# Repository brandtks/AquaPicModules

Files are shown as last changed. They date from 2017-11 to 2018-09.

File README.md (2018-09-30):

README
======
Board design and firmware for all modules used with the AquaPic Aquarium Controller. Each board should have corresponding firmware that works with that board version. All modules communicate with and are controlled by the [master controller/head unit](https://github.com/AquaPic/AquaPicController).

 * All PCB designs and layouts including gerber files are located under the _Boards_ directory. All PCB design is done using [KiCAD](http://kicad-pcb.org/). 
 * Firmware is located in the _Firmware_ directory. All the card's firmware should build without the need of the [MPLAB X IDE](http://www.microchip.com/mplab/mplab-x-ide), just the [XC compilers](http://www.microchip.com/mplab/compilers).
 * The _Documentation_ directory contains some useful information such as AquaPic Bus packets and other random notes.
 * Bill of materials are shared in [Google Drive](https://drive.google.com/drive/folders/1AOH0jgJ0CXvZnuD189EO4B9ZkvwggwkB?usp=sharing). 

### Status 
**IMPORTANT**: All modules are a work in progress. Most, if not all, are untested and very alpha quality.

### Website 
[HackADay Build Log](https://hackaday.io/project/1436-aquapic-aquarium-controller)

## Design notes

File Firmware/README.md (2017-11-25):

README
======
Firmware for the input/output cards for the AquaPic aquarium controller. Includes Analog Input and Output, Digital Input, and Power Strip stored in the projects directory. Libraries are included in the lib directory. This inludes the AquaPicBus slave driver, some common macros, and PIC16F specific drivers for ADC, UART, and PWM. All modules communicate with and are controlled by the [master controller/head unit](https://github.com/AquaPic/AquaPicController).

### Status
**IMPORTANT**: All modules are a work in progress. Most, if not all, are untested and very alpha quality.

### Toolchain
 * [Microchip XC8 v1.43](http://www.microchip.com/mplab/compilers); may work with early versions.
 * [Microchip XC32 v1.44](http://www.microchip.com/mplab/compilers); may work with early versions.

### Building
Edit Makefile-define.mk to match the executing environment and desired output paths, then exectute ```make```.

### License
The AquaPic firmware code is released under the terms of the GNU General Public License (GPL), version 3 or later. See COPYING for details.

### Website
 * [HackADay Build Log](https://hackaday.io/project/1436-aquapic-aquarium-controller)

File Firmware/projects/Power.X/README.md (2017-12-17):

README
======
Firmware for Power version 6. _libmmc.a_ contains the object files compiled from the code generated by the Microchip Code Configurator v3 utility. The object files were built used XC32 v1.44. 

### Status
**IMPORTANT**: Work in progress. Probably untested and very alpha quality.

### Website
 * [HackADay Build Log](https://hackaday.io/project/1436-aquapic-aquarium-controller)

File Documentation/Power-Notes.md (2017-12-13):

### Notes
 * Removed current measuring circuit from main control board, because it was a pain to design around. Instead, current monitoring will be done on a separate board that plugs into the control board.

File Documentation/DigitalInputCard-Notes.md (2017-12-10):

### Notes
 * The charlieplexed LEDs operate at 166.67Hz. This leads to each led being on for 1ms and off for 5ms.
 * The LEDs chosen have an forward voltage of approximately 3.1 V at 12 mA. 
 * With a 1/6 duty cycle the effective current will be 2 mA which results in a 20 mcd luminous intensity.

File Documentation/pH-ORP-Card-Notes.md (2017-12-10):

### Notes
 * The load resister on the output of the isolation power supply can and probably will be left off. Its there just in case stability is an issue.
 * The mosfet prior to each of the isolation power supplies provides a way to disable a channel when not in use thus limiting overall current draw.

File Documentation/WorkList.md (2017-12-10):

Bugs
=====================
 * Can't add modules, errors on address already used, only on the raspberry pi 
 * Move setup to init function and add input checking

Main Controller Software
========================
## Worklist 
 * Add way to change LPF constant for AI and pH/ORP
 * Enable/disable channels for pH
 * pH/ORP Scene
 * pH/ORP calibration
 * Refactor ATO to separate module
 * Add ATO scene
 * RO/DI module
 * Saltwater mixing module
 * Wave module
 * Add/Move widgets to home screen at runtime
 * Remove cards, power strips at runtime
 * Notifications
 * Tank maintenance scheduler
 * Runtime modules
 * Data logging on server
 * Backup/Store settings on database
 * Low priority - Lighting return to auto (ramp/hold to auto setpoint) and shutdown
 * _Maybe_ - Continue moving from list to dictionary in driver

Peripherals
===========
## Analog Input 
#### Firmware
 * Test on a board
 * Enable/disable channels
#### Hardware

## Analog Output
#### Firmware
 * Test on a board
#### Hardware
 * Test selectable output prior to manufacturing boards

## Digital Input
#### Firmware
 * Test on a board
#### Hardware

## pH/ORP 
#### Firmware
 * Test on a board
#### Hardware

## Power
#### Firmware
 * Refactor processor to PIC32MM0064GPM***
#### Hardware
 * Refactor processor to PIC32MM0064GPM***

Long Range Goals
================
 * Look at outlet current of heaters to determine what the setpoint of the heater is currently set at and then also check for stuck heater. 
 * Home server for data logging, and website. Home server will also issues commands to controller.
 * Pump control card
 * Water change module
 * Dosing Pumps
 * Feeding
 * Salinity
 * Function block programming
 * Move modules and GUI to ‘plugins’ that are added at runtime. This will allow the controller to be used for any sort of home automation such as home brewing, gardening, aquaponics. 
 * Over the “air” updates and boot loader for all slave modules

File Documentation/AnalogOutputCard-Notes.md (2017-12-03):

### Notes
 * The way the PWM(capture) module is implemented in the PIC32MM, there is a tradeoff between frequency and resolution. As the PWM frequency is increased, there is less range before the timer rolls over. To allow for changing the frequency in the firmware the main controller will send a value of 0 to 100 instead of some direct bit value. 
 * Currently the frequecy is set to 2Khz. With the capture module clocked to the system frequency at 24KHz, the timer rolls over at 0x4B0, 1200, i.e. 1200 bits of resolution.
 * CCPxRA will always remain at 0. CCPxRB is used to adjust the duty cycle.

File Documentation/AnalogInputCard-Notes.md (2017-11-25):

### Notes
 * Switched to PIC32MM0064GPM028 because there will be quite a bit of 16 and 32 bit math including division. The PIC16F is terrible at this especially with the free compiler.
 * Using bi-directional level shifts for the TX/RX lines, because it seems to be the cheapest option. 

### Voltage divider protection:
Vout = (Vin * 10) / (14.99 + RVx)
The voltage divider servers two purposes: 
 * First it limits current and 
 * Second it can be used to increase the measured voltage because most sensor devices don't output 5Vdc at full range. However, this is still limited. With RVx at 0R the minimum input voltage to reach full scale is 3.07V.

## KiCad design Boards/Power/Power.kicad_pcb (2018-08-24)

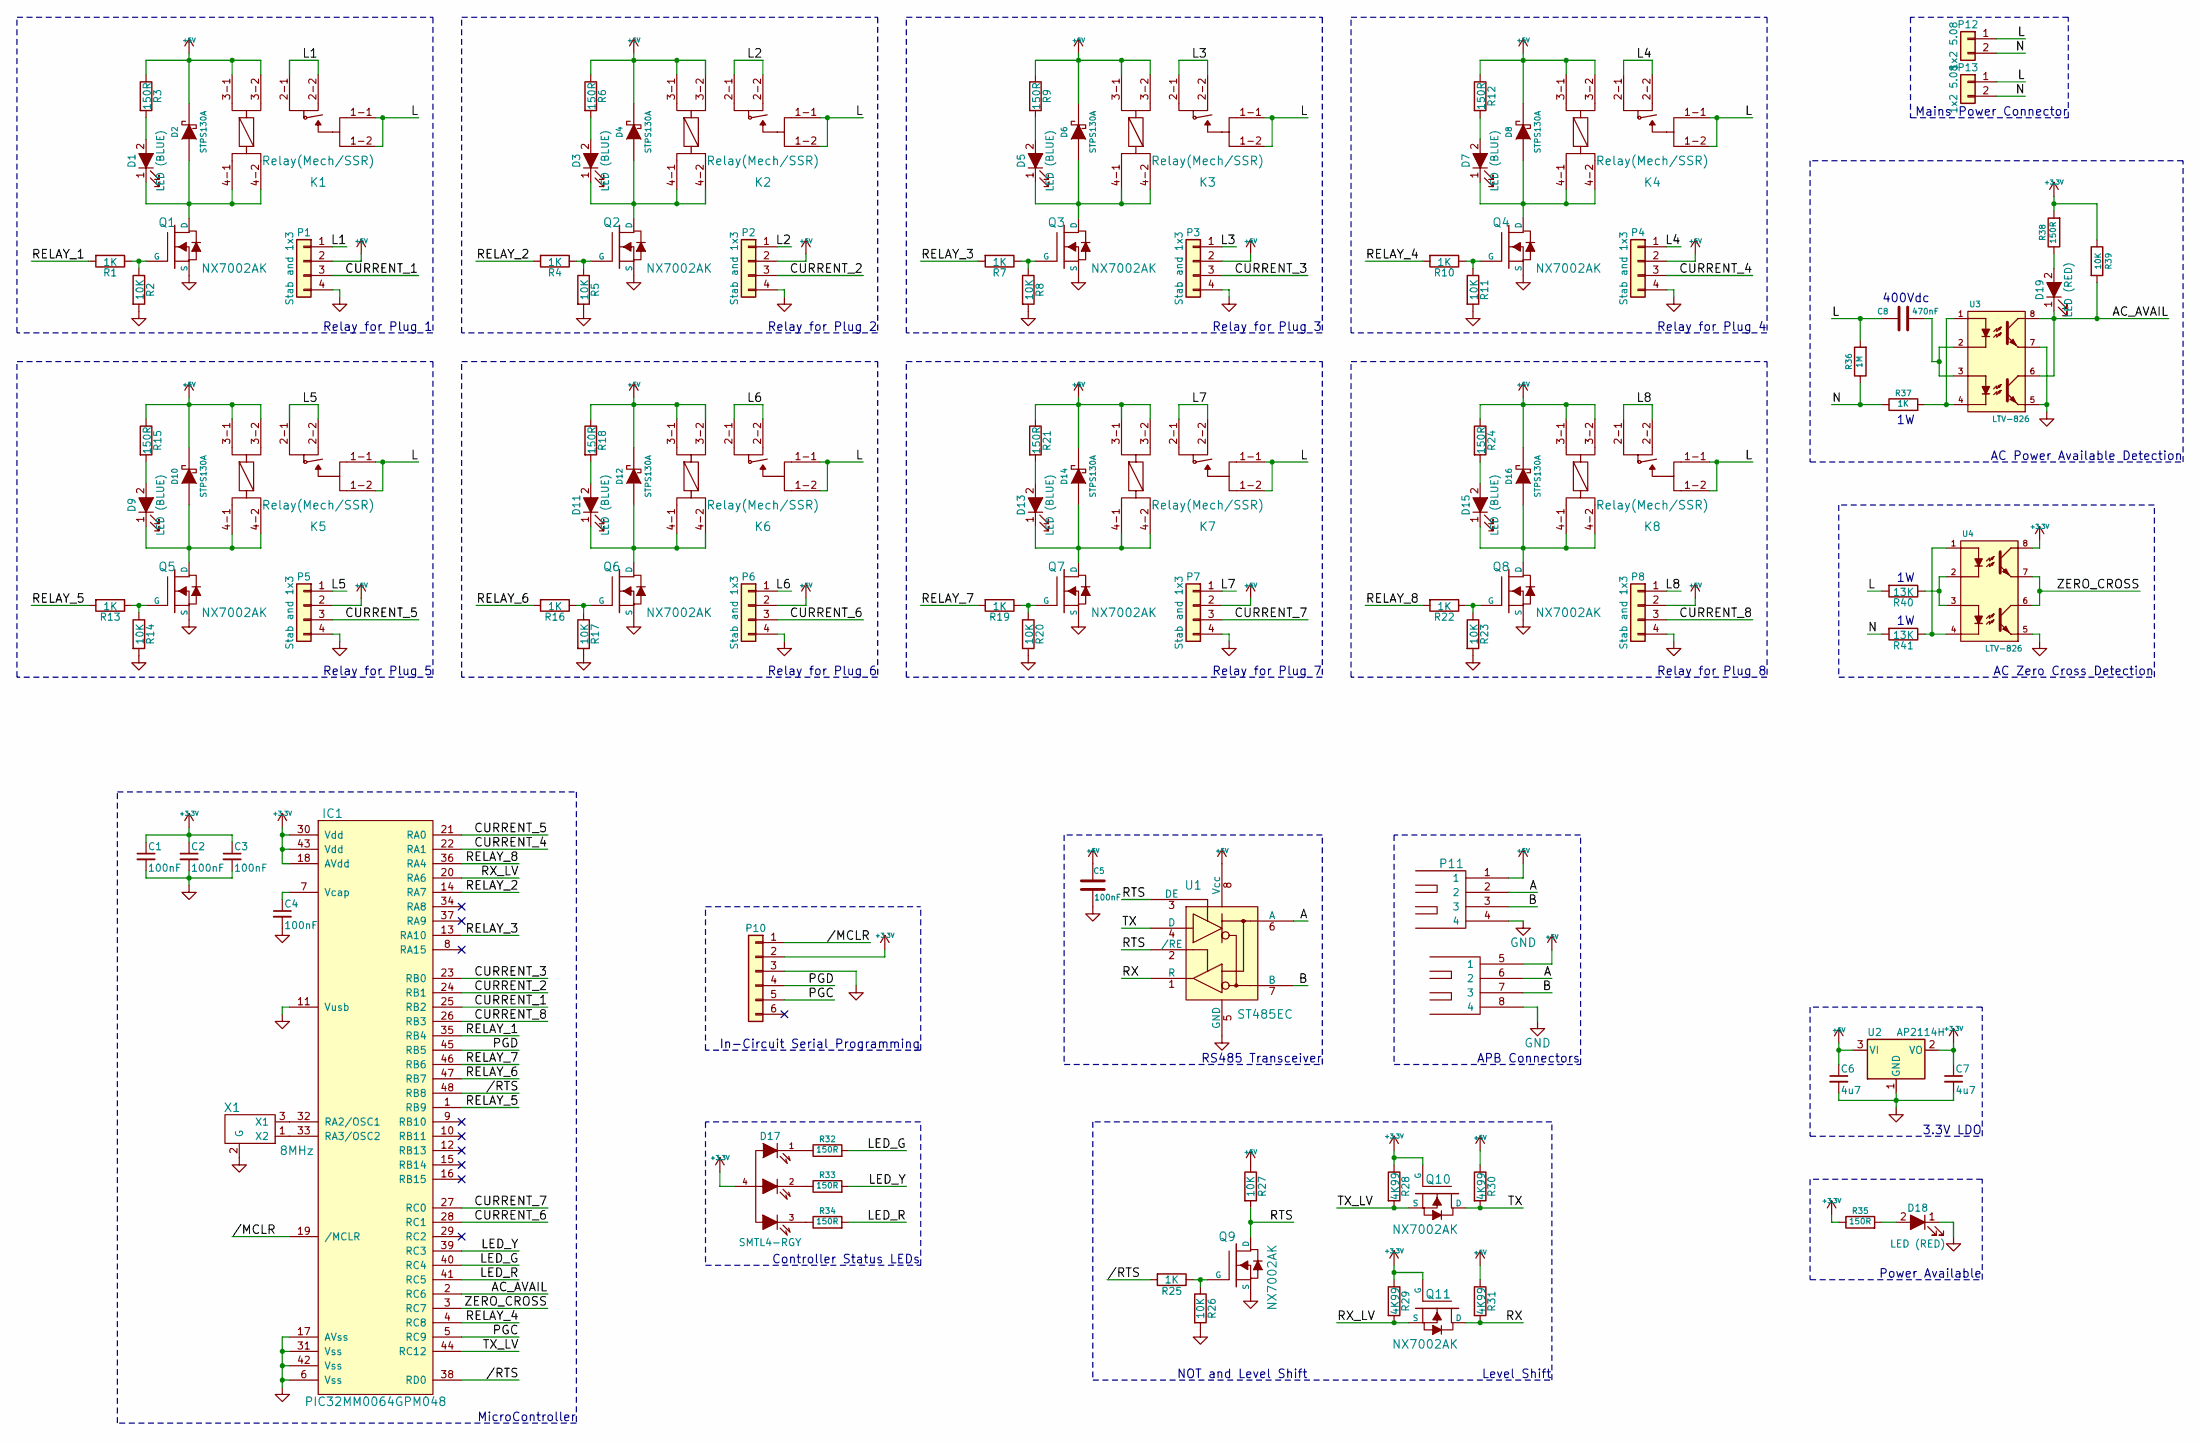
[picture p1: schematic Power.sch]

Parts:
C1, C2, C3, C4, C5: 100nF; C_0805
C6, C7: 4u7; C_0805
C8: 470nF; C_1812
D1, D3, D5, D7, D9, D11, D13, D15: LED (BLUE); LED_0805
D2, D4, D6, D8, D10, D12, D14, D16: STPS130A; D_SMA
D17: SMTL4-RGY; PLCC-4
D18, D19: LED (RED); LED_0805
IC1: PIC32MM0064GPM048; TQFP-48_7x7mm_Pitch0.5mm; Manufacter Part Number PIC32MM0064GPM048T-I/PT
K1, K2, K3, K4, K5, K6, K7, K8: Relay(Mech/SSR); Relay-Mech-SSR
P1, P2, P3, P4, P5, P6, P7, P8: Stab and 1x3; Current_Board
P10: 1x6 2.54 Pin Header; Pin_Header_Straight_1x06_Pitch2.54mm
P11: Stacked USBA; USB-1.1_Stacked
P12, P13: 1x2 5.08; Screw_Header_1x2_5.08
Q1, Q2, Q3, Q4, Q5, Q6, Q7, Q8, Q9, Q10, Q11: NX7002AK; SOT-23
R1, R4, R7, R10, R13, R16, R19, R22, R25: 1K; R_0805
R2, R5, R8, R11, R14, R17, R20, R23, R26, R27, R39: 10K; R_0805
R3, R6, R9, R12, R15, R18, R21, R24, R32, R33, R34, R35, R38: 150R; R_0805
R28, R29, R30, R31: 4K99; R_0805
R36: 1M; R_2010
R37: 1K; R_2512
R40, R41: 13K; R_2512
U1: ST485EC; SOIC-8_3.9x4.9mm_Pitch1.27mm
U2: AP2114H; SOT-223
U3, U4: LTV-826; 8_SMD_GULL_WING
X1: 8MHz; Resonator_3.2x1.3

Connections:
+3V3: C1.1, C2.1, C3.1, C7.1, D17.4, IC1.18 (AVdd), IC1.30 (Vdd), IC1.43 (Vdd), P10.2, Q10.1 (G), Q11.1 (G), R28.1, R29.1, R35.1, R38.2, R39.1, U2.2 (VO), U4.8; also elsewhere on the board
+5V: C5.1, C6.1, D2.2 (K), D4.2 (K), D6.2 (K), D8.2 (K), D10.2 (K), D12.2 (K), D14.2 (K), D16.2 (K), K1.3-1, K1.3-2, K2.3-1, K2.3-2, K3.3-1, K3.3-2, K4.3-1, K4.3-2, K5.3-1, K5.3-2, K6.3-1, K6.3-2, K7.3-1, K7.3-2, K8.3-1, K8.3-2, P1.2, P2.2, P3.2, P4.2, P5.2, P6.2, P7.2, P8.2, P11.1, P11.5 (1), R3.1, R6.1, R9.1, R12.1, R15.1, R18.1, R21.1, R24.1, R27.1, R30.1, R31.1, U1.8 (Vcc), U2.3 (VI)
//MCLR: IC1.19 (/MCLR), P10.1; also elsewhere on the board
//RTS: IC1.38 (RD0), IC1.48 (RB8), R25.2
/A: P11.2, P11.6 (2), U1.6 (A)
/AC_AVAIL: D19.1 (K), IC1.2 (RC6), R39.2, U3.6, U3.8
/B: P11.3, P11.7 (3), U1.7 (B)
/CURRENT_1: IC1.25 (RB2), P1.3
/CURRENT_2: IC1.24 (RB1), P2.3
/CURRENT_3: IC1.23 (RB0), P3.3
/CURRENT_4: IC1.22 (RA1), P4.3
/CURRENT_5: IC1.21 (RA0), P5.3
/CURRENT_6: IC1.28 (RC1), P6.3
/CURRENT_7: IC1.27 (RC0), P7.3
/CURRENT_8: IC1.26 (RB3), P8.3
/L: C8.1, K1.1-1, K1.1-2, K2.1-1, K2.1-2, K3.1-1, K3.1-2, K4.1-1, K4.1-2, K5.1-1, K5.1-2, K6.1-1, K6.1-2, K7.1-1, K7.1-2, K8.1-1, K8.1-2, P12.1, P13.1, R36.2, R40.2
/L1: K1.2-1, K1.2-2, P1.1
/L2: K2.2-1, K2.2-2, P2.1
/L3: K3.2-1, K3.2-2, P3.1
/L4: K4.2-1, K4.2-2, P4.1
/L5: K5.2-1, K5.2-2, P5.1
/L6: K6.2-1, K6.2-2, P6.1
/L7: K7.2-1, K7.2-2, P7.1
/L8: K8.2-1, K8.2-2, P8.1
/LED_G: IC1.40 (RC4), R32.2
/LED_R: IC1.41 (RC5), R34.2
/LED_Y: IC1.39 (RC3), R33.2
/N: P12.2, P13.2, R36.1, R37.1, R41.2
/PGC: IC1.5 (RC9), P10.5; also elsewhere on the board
/PGD: IC1.45 (RB5), P10.4; also elsewhere on the board
/RELAY_1: IC1.35 (RB4), R1.2
/RELAY_2: IC1.14 (RA7), R4.2
/RELAY_3: IC1.13 (RA10), R7.2
/RELAY_4: IC1.4 (RC8), R10.2
/RELAY_5: IC1.1 (RB9), R13.2
/RELAY_6: IC1.47 (RB7), R16.2
/RELAY_7: IC1.46 (RB6), R19.2
/RELAY_8: IC1.36 (RA4), R22.2
/RTS: Q9.3 (D), R27.2, U1.2 (/RE), U1.3 (DE)
/RX: Q11.3 (D), R31.2, U1.1 (R)
/RX_LV: IC1.20 (RA6), Q11.2 (S), R29.2
/TX: Q10.3 (D), R30.2, U1.4 (D)
/TX_LV: IC1.44 (RC12), Q10.2 (S), R28.2
/ZERO_CROSS: IC1.3 (RC7), U4.6, U4.7
GND: C1.2, C2.2, C3.2, C4.2, C5.2, C6.2, C7.2, D18.1 (K), IC1.6 (Vss), IC1.11 (Vusb), IC1.17 (AVss), IC1.31 (Vss), IC1.42 (Vss), P1.4, P2.4, P3.4, P4.4, P5.4, P6.4, P7.4, P8.4, P10.3, P11.4, P11.8 (4), Q1.2 (S), Q2.2 (S), Q3.2 (S), Q4.2 (S), Q5.2 (S), Q6.2 (S), Q7.2 (S), Q8.2 (S), Q9.2 (S), R2.2, R5.2, R8.2, R11.2, R14.2, R17.2, R20.2, R23.2, R26.2, U1.5 (GND), U2.1 (GND), U3.5, U3.7, U4.5, X1.2 (G); also elsewhere on the board
unnamed: C4.1, IC1.7 (Vcap)
unnamed: C8.2, U3.2, U3.3
unnamed: D1.1 (K), D2.1 (A), K1.4-1, K1.4-2, Q1.3 (D)
unnamed: D1.2 (A), R3.2
unnamed: D3.1 (K), D4.1 (A), K2.4-1, K2.4-2, Q2.3 (D)
unnamed: D3.2 (A), R6.2
unnamed: D5.1 (K), D6.1 (A), K3.4-1, K3.4-2, Q3.3 (D)
unnamed: D5.2 (A), R9.2
unnamed: D7.1 (K), D8.1 (A), K4.4-1, K4.4-2, Q4.3 (D)
unnamed: D7.2 (A), R12.2
unnamed: D9.2 (A), R15.2
unnamed: D9.1 (K), D10.1 (A), K5.4-1, K5.4-2, Q5.3 (D)
unnamed: D11.1 (K), D12.1 (A), K6.4-1, K6.4-2, Q6.3 (D)
unnamed: D11.2 (A), R18.2
unnamed: D13.1 (K), D14.1 (A), K7.4-1, K7.4-2, Q7.3 (D)
unnamed: D13.2 (A), R21.2
unnamed: D15.1 (K), D16.1 (A), K8.4-1, K8.4-2, Q8.3 (D)
unnamed: D15.2 (A), R24.2
unnamed: D17.1, R32.1
unnamed: D17.2, R33.1
unnamed: D17.3, R34.1
unnamed: D18.2 (A), R35.2
unnamed: D19.2 (A), R38.1
unnamed: IC1.32 (RA2/OSC1), X1.3 (X1)
unnamed: IC1.33 (RA3/OSC2), X1.1 (X2)
unnamed: Q1.1 (G), R1.1, R2.1
unnamed: Q2.1 (G), R4.1, R5.1
unnamed: Q3.1 (G), R7.1, R8.1
unnamed: Q4.1 (G), R10.1, R11.1
unnamed: Q5.1 (G), R13.1, R14.1
unnamed: Q6.1 (G), R16.1, R17.1
unnamed: Q7.1 (G), R19.1, R20.1
unnamed: Q8.1 (G), R22.1, R23.1
unnamed: Q9.1 (G), R25.1, R26.1
unnamed: R37.2, U3.1, U3.4
unnamed: R40.1, U4.2, U4.3
unnamed: R41.1, U4.1, U4.4

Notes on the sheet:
400Vdc
AC Power Available Detection
Mains Power Connector
AC Zero Cross Detection
In-Circuit Serial Programming
MicroController
Controller Status LEDs
RS485 Transceiver
APB Connectors
Level Shift
NOT and Level Shift
3.3V LDO
Power Available
Relay for Plug 1
Relay for Plug 2
Relay for Plug 3
Relay for Plug 4
Relay for Plug 5
Relay for Plug 6
Relay for Plug 7
Relay for Plug 8

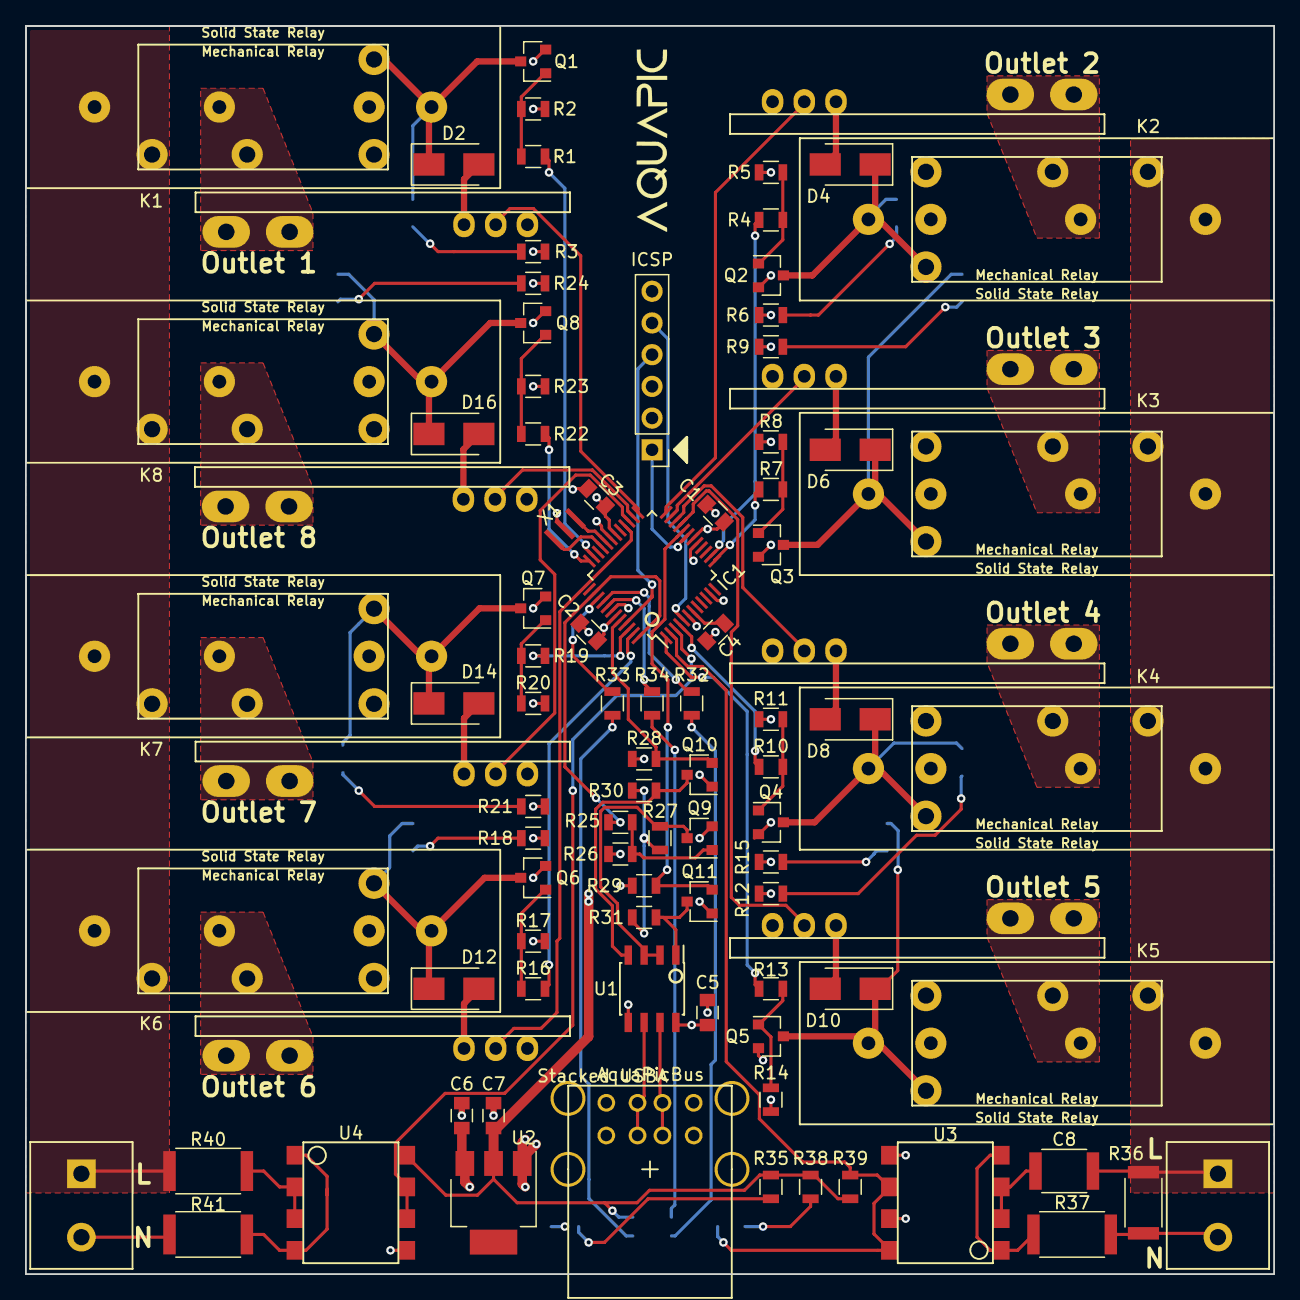
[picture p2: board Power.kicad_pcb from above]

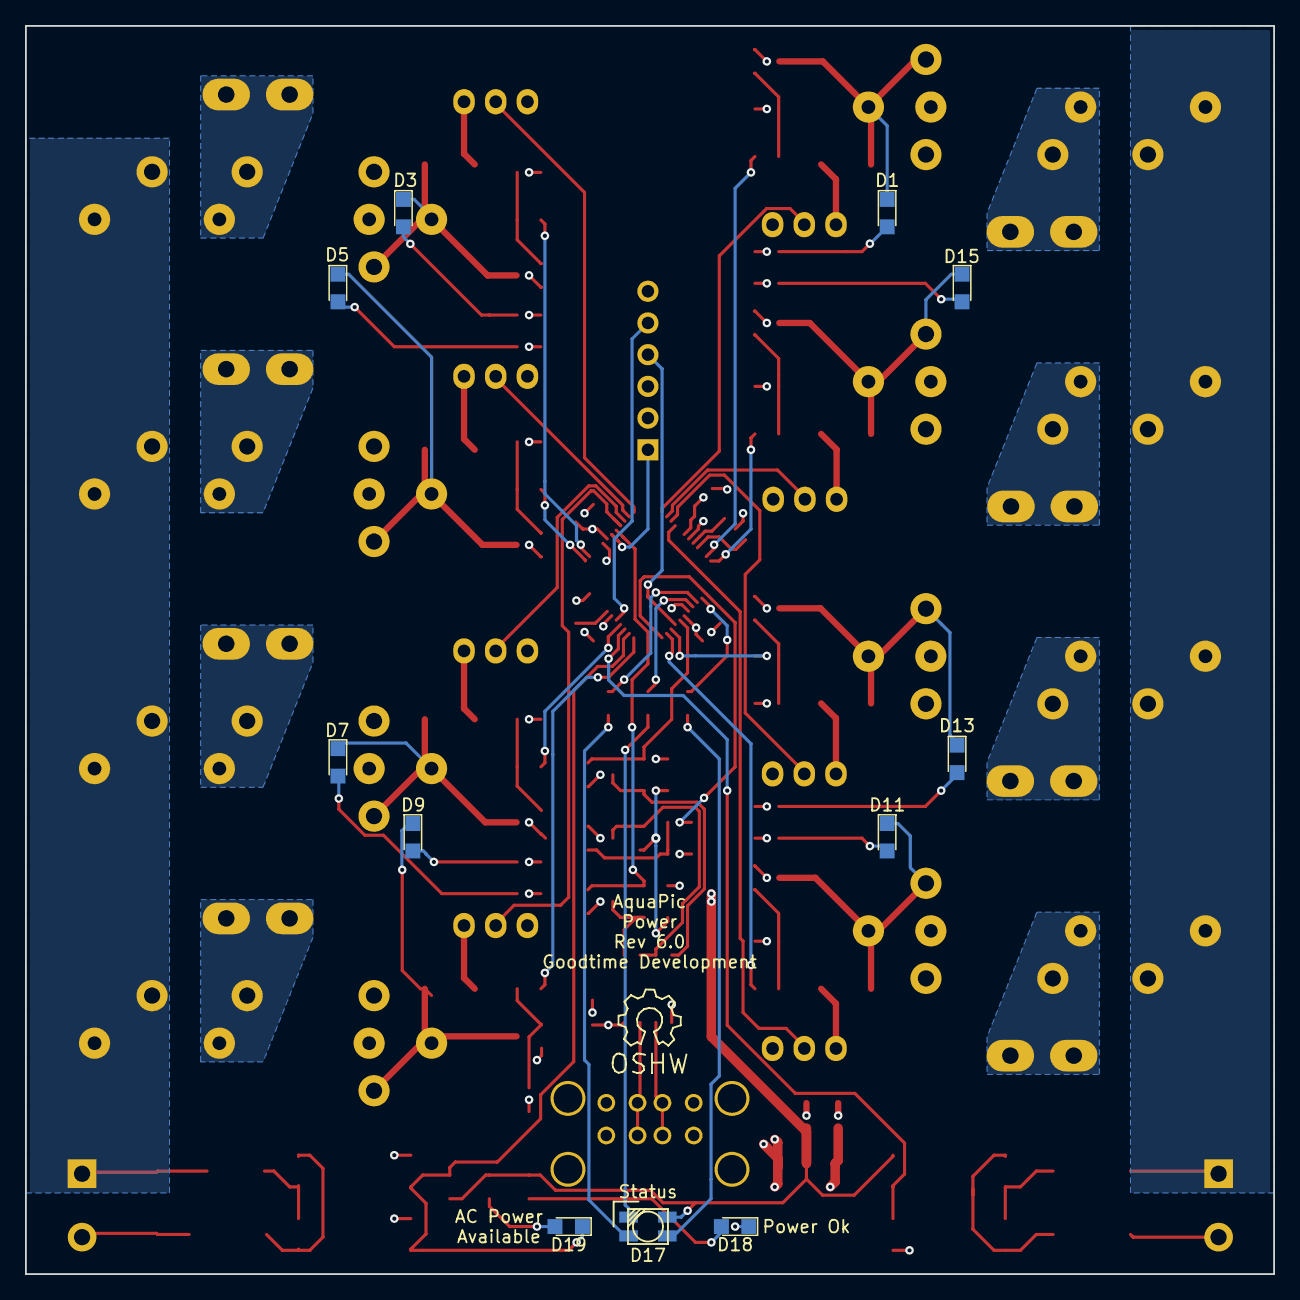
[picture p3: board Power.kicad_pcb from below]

Board: 4 copper layers, 100.0 x 100.0 mm, 105 parts (11 on the bottom side), 82 nets.

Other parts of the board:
ICSP: 1x6 2.54 Pin Header; Pin_Header_Straight_1x06_Pitch2.54mm

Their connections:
+3V3: ICSP.2; also elsewhere on the board
//MCLR: ICSP.1; also elsewhere on the board
/PGC: ICSP.5; also elsewhere on the board
/PGD: ICSP.4; also elsewhere on the board
GND: ICSP.3; also elsewhere on the board

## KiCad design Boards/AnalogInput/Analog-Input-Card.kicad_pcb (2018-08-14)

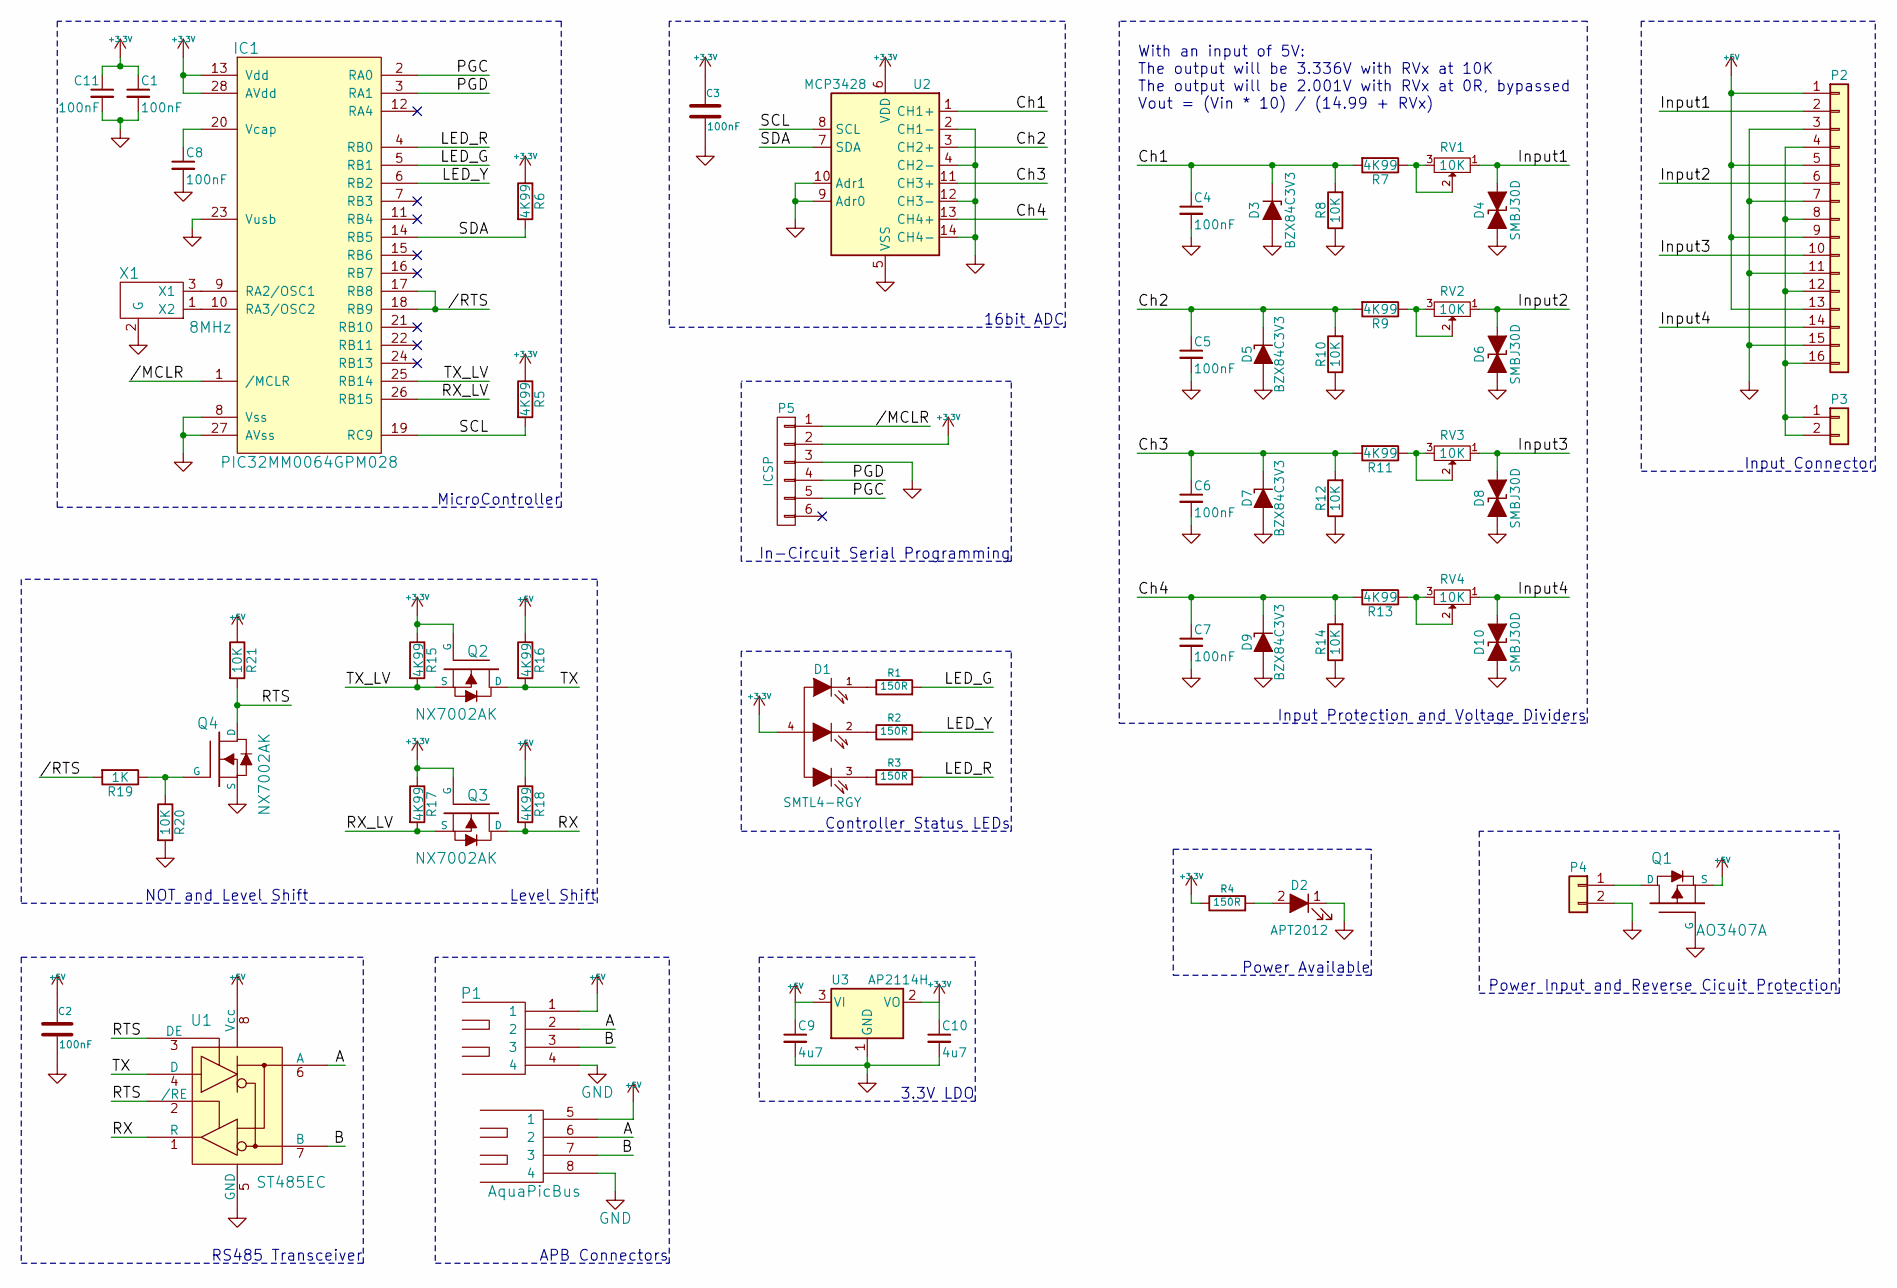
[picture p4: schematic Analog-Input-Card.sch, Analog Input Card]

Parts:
C1, C2, C3, C4, C5, C6, C7, C8, C11: 100nF; C_0805
C9, C10: 4u7; C_0805
D1: SMTL4-RGY; PLCC-4
D2: APT2012; LED-0805
D3, D5, D7, D9: BZX84C3V3; D_SOT-23_ANK
D4, D6, D8, D10: SMBJ30D; D_SMB
IC1: PIC32MM0064GPM028; SSOP-28_5.3x10.2mm_Pitch0.65mm
P1: AquaPicBus; USB-1.1_Stacked
P2: 1x16 2.54; Screw_Header_1x16
P3, P4: 1x2 2.54; Screw_Header_1x2
P5: ICSP; Pin_Header_Straight_1x06_Pitch2.54mm
Q1: AO3407A; SOT-23
Q2, Q3, Q4: NX7002AK; SOT-23
R1, R2, R3, R4: 150R; R_0805
R5, R6, R7, R9, R11, R13, R15, R16, R17, R18: 4K99; R_0805
R8, R10, R12, R14, R20, R21: 10K; R_0805
R19: 1K; R_0805
RV1, RV2, RV3, RV4: 10K; POTENTIAMETER_SMD
U1: ST485EC; SOIC-8_3.9x4.9mm_Pitch1.27mm
U2: MCP3428; TSSOP-14_4.4x5mm_Pitch0.65mm
U3: AP2114H; SOT-223
X1: 8MHz; Resonator_3.2x1.3

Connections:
+3V3: C1.1, C3.1, C10.1, C11.1, D1.4, IC1.13 (Vdd), IC1.28 (AVdd), P5.2, Q2.1 (G), Q3.1 (G), R4.1, R5.1, R6.1, R15.1, R17.1, U2.6 (VDD), U3.2 (VO); also elsewhere on the board
+5V: C2.1, C9.1, P1.1, P1.5 (1), P2.1, P2.5, P2.9, P2.13, Q1.2 (S), R16.1, R18.1, R21.1, U1.8 (Vcc), U3.3 (VI)
//MCLR: IC1.1 (/MCLR), P5.1; also elsewhere on the board
//RTS: IC1.17 (RB8), IC1.18 (RB9), R19.2
/A: P1.2, P1.6 (2), U1.6 (A)
/B: P1.3, P1.7 (3), U1.7 (B)
/Ch1: C4.1, D3.1 (K), R7.2, R8.2, U2.1 (CH1+)
/Ch2: C5.1, D5.1 (K), R9.2, R10.2, U2.3 (CH2+)
/Ch3: C6.1, D7.1 (K), R11.2, R12.2, U2.11 (CH3+)
/Ch4: C7.1, D9.1 (K), R13.2, R14.2, U2.13 (CH4+)
/Input1: D4.1 (A1), P2.2, RV1.1
/Input2: D6.1 (A1), P2.6, RV2.1
/Input3: D8.1 (A1), P2.10, RV3.1
/Input4: D10.1 (A1), P2.14, RV4.1
/LED_G: IC1.5 (RB1), R1.2
/LED_R: IC1.4 (RB0), R3.2
/LED_Y: IC1.6 (RB2), R2.2
/PGC: IC1.2 (RA0), P5.5; also elsewhere on the board
/PGD: IC1.3 (RA1), P5.4; also elsewhere on the board
/RTS: Q4.3 (D), R21.2, U1.2 (/RE), U1.3 (DE)
/RX: Q3.3 (D), R18.2, U1.1 (R)
/RX_LV: IC1.26 (RB15), Q3.2 (S), R17.2
/SCL: IC1.19 (RC9), R5.2, U2.8 (SCL)
/SDA: IC1.14 (RB5), R6.2, U2.7 (SDA)
/TX: Q2.3 (D), R16.2, U1.4 (D)
/TX_LV: IC1.25 (RB14), Q2.2 (S), R15.2
GND: C1.2, C2.2, C3.2, C4.2, C5.2, C6.2, C7.2, C8.2, C9.2, C10.2, C11.2, D2.1 (K), D3.2 (A), D4.2 (A2), D5.2 (A), D6.2 (A2), D7.2 (A), D8.2 (A2), D9.2 (A), D10.2 (A2), IC1.8 (Vss), IC1.23 (Vusb), IC1.27 (AVss), P1.4, P1.8 (4), P2.3, P2.7, P2.11, P2.15, P4.2, P5.3, Q1.1 (G), Q4.2 (S), R8.1, R10.1, R12.1, R14.1, R20.2, U1.5 (GND), U2.2 (CH1-), U2.4 (CH2-), U2.5 (VSS), U2.9 (Adr0), U2.10 (Adr1), U2.12 (CH3-), U2.14 (CH4-), U3.1 (GND), X1.2 (G); also elsewhere on the board
unnamed: C8.1, IC1.20 (Vcap)
unnamed: D1.1, R1.1
unnamed: D1.2, R2.1
unnamed: D1.3, R3.1
unnamed: D2.2 (A), R4.2
unnamed: IC1.9 (RA2/OSC1), X1.3 (X1)
unnamed: IC1.10 (RA3/OSC2), X1.1 (X2)
unnamed: P2.4, P2.8, P2.12, P2.16, P3.1, P3.2
unnamed 43: P4.1, Q1.3 (D); also elsewhere on the board
unnamed: Q4.1 (G), R19.1, R20.1
unnamed: R7.1, RV1.2, RV1.3
unnamed: R9.1, RV2.2, RV2.3
unnamed: R11.1, RV3.2, RV3.3
unnamed: R13.1, RV4.2, RV4.3

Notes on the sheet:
In-Circuit Serial Programming
MicroController
Input Connector
RS485 Transceiver
Power Input and Reverse Cicuit Protection
APB Connectors
16bit ADC
Input Protection and Voltage Dividers
With an input of 5V: The output will be 3.336V with RVx at 10K The output will be 2.001V with RVx at 0R, bypassed Vout = (Vin * 10) / (14.99 + RVx)
Level Shift
NOT and Level Shift
3.3V LDO
Controller Status LEDs
Power Available

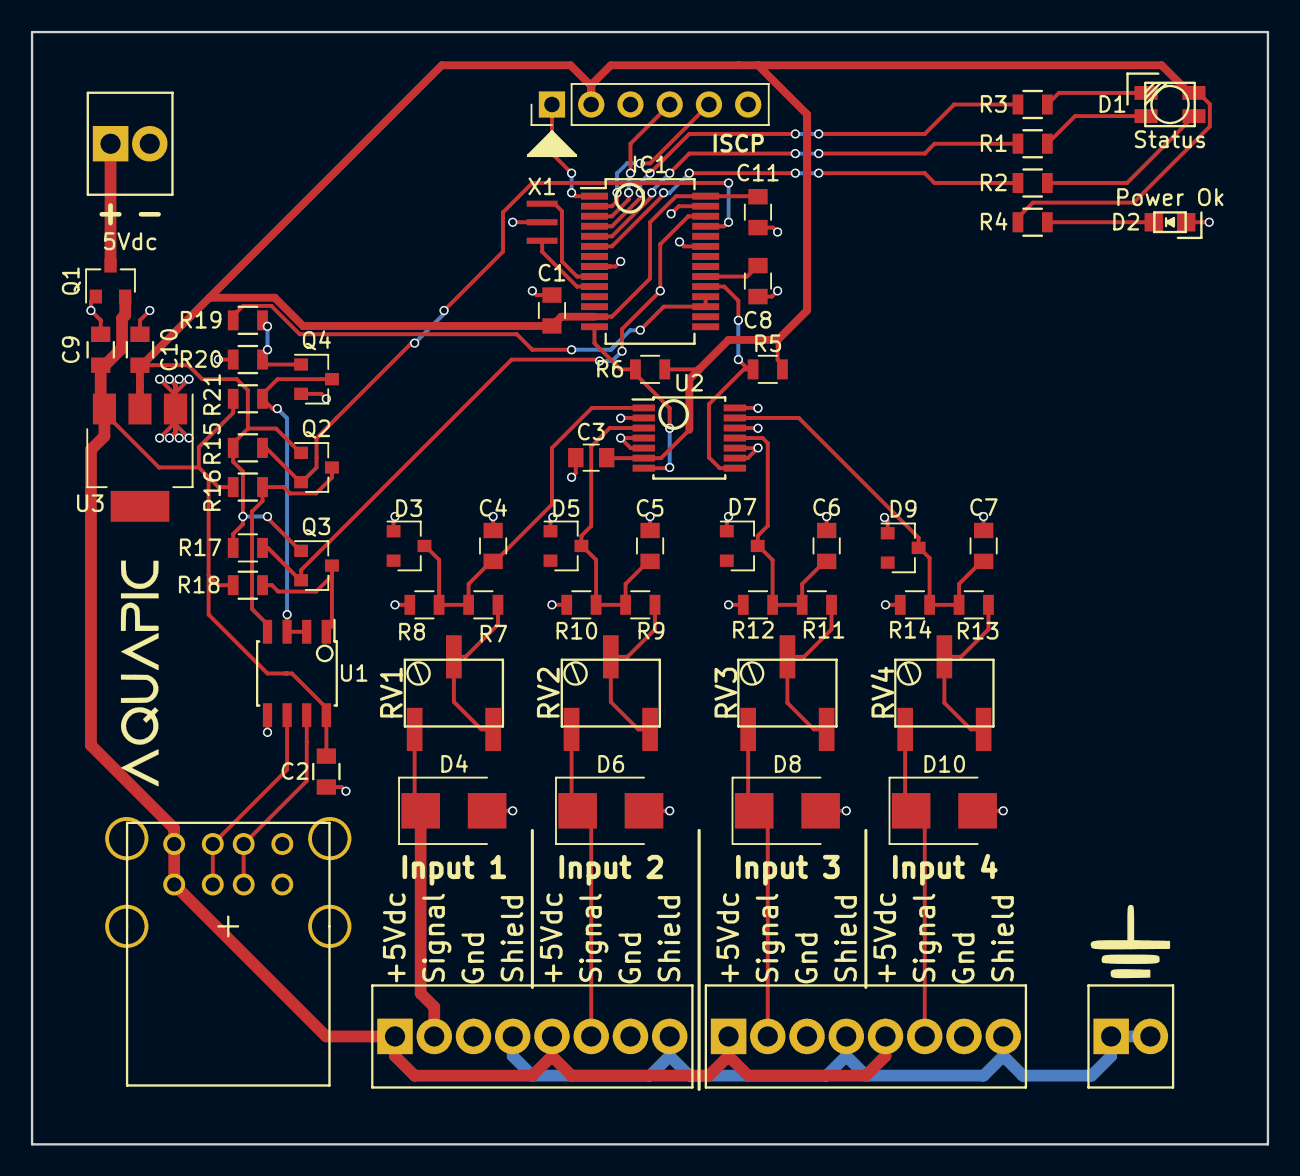
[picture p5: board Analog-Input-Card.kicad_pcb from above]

Board: 2 copper layers, 80.0 x 72.0 mm, 60 parts (0 on the bottom side), 41 nets.

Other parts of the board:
5Vdc: 2x1 2.54; Screw_Header_1x2
P1#2: 6x1 2.54; Pin_Header_Straight_1x06_Pitch2.54mm

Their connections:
+3V3: P1#2.2; also elsewhere on the board
//MCLR: P1#2.1; also elsewhere on the board
/PGC: P1#2.5; also elsewhere on the board
/PGD: P1#2.4; also elsewhere on the board
GND: 5Vdc.2, P1#2.3; also elsewhere on the board
unnamed 43: 5Vdc.1; also elsewhere on the board

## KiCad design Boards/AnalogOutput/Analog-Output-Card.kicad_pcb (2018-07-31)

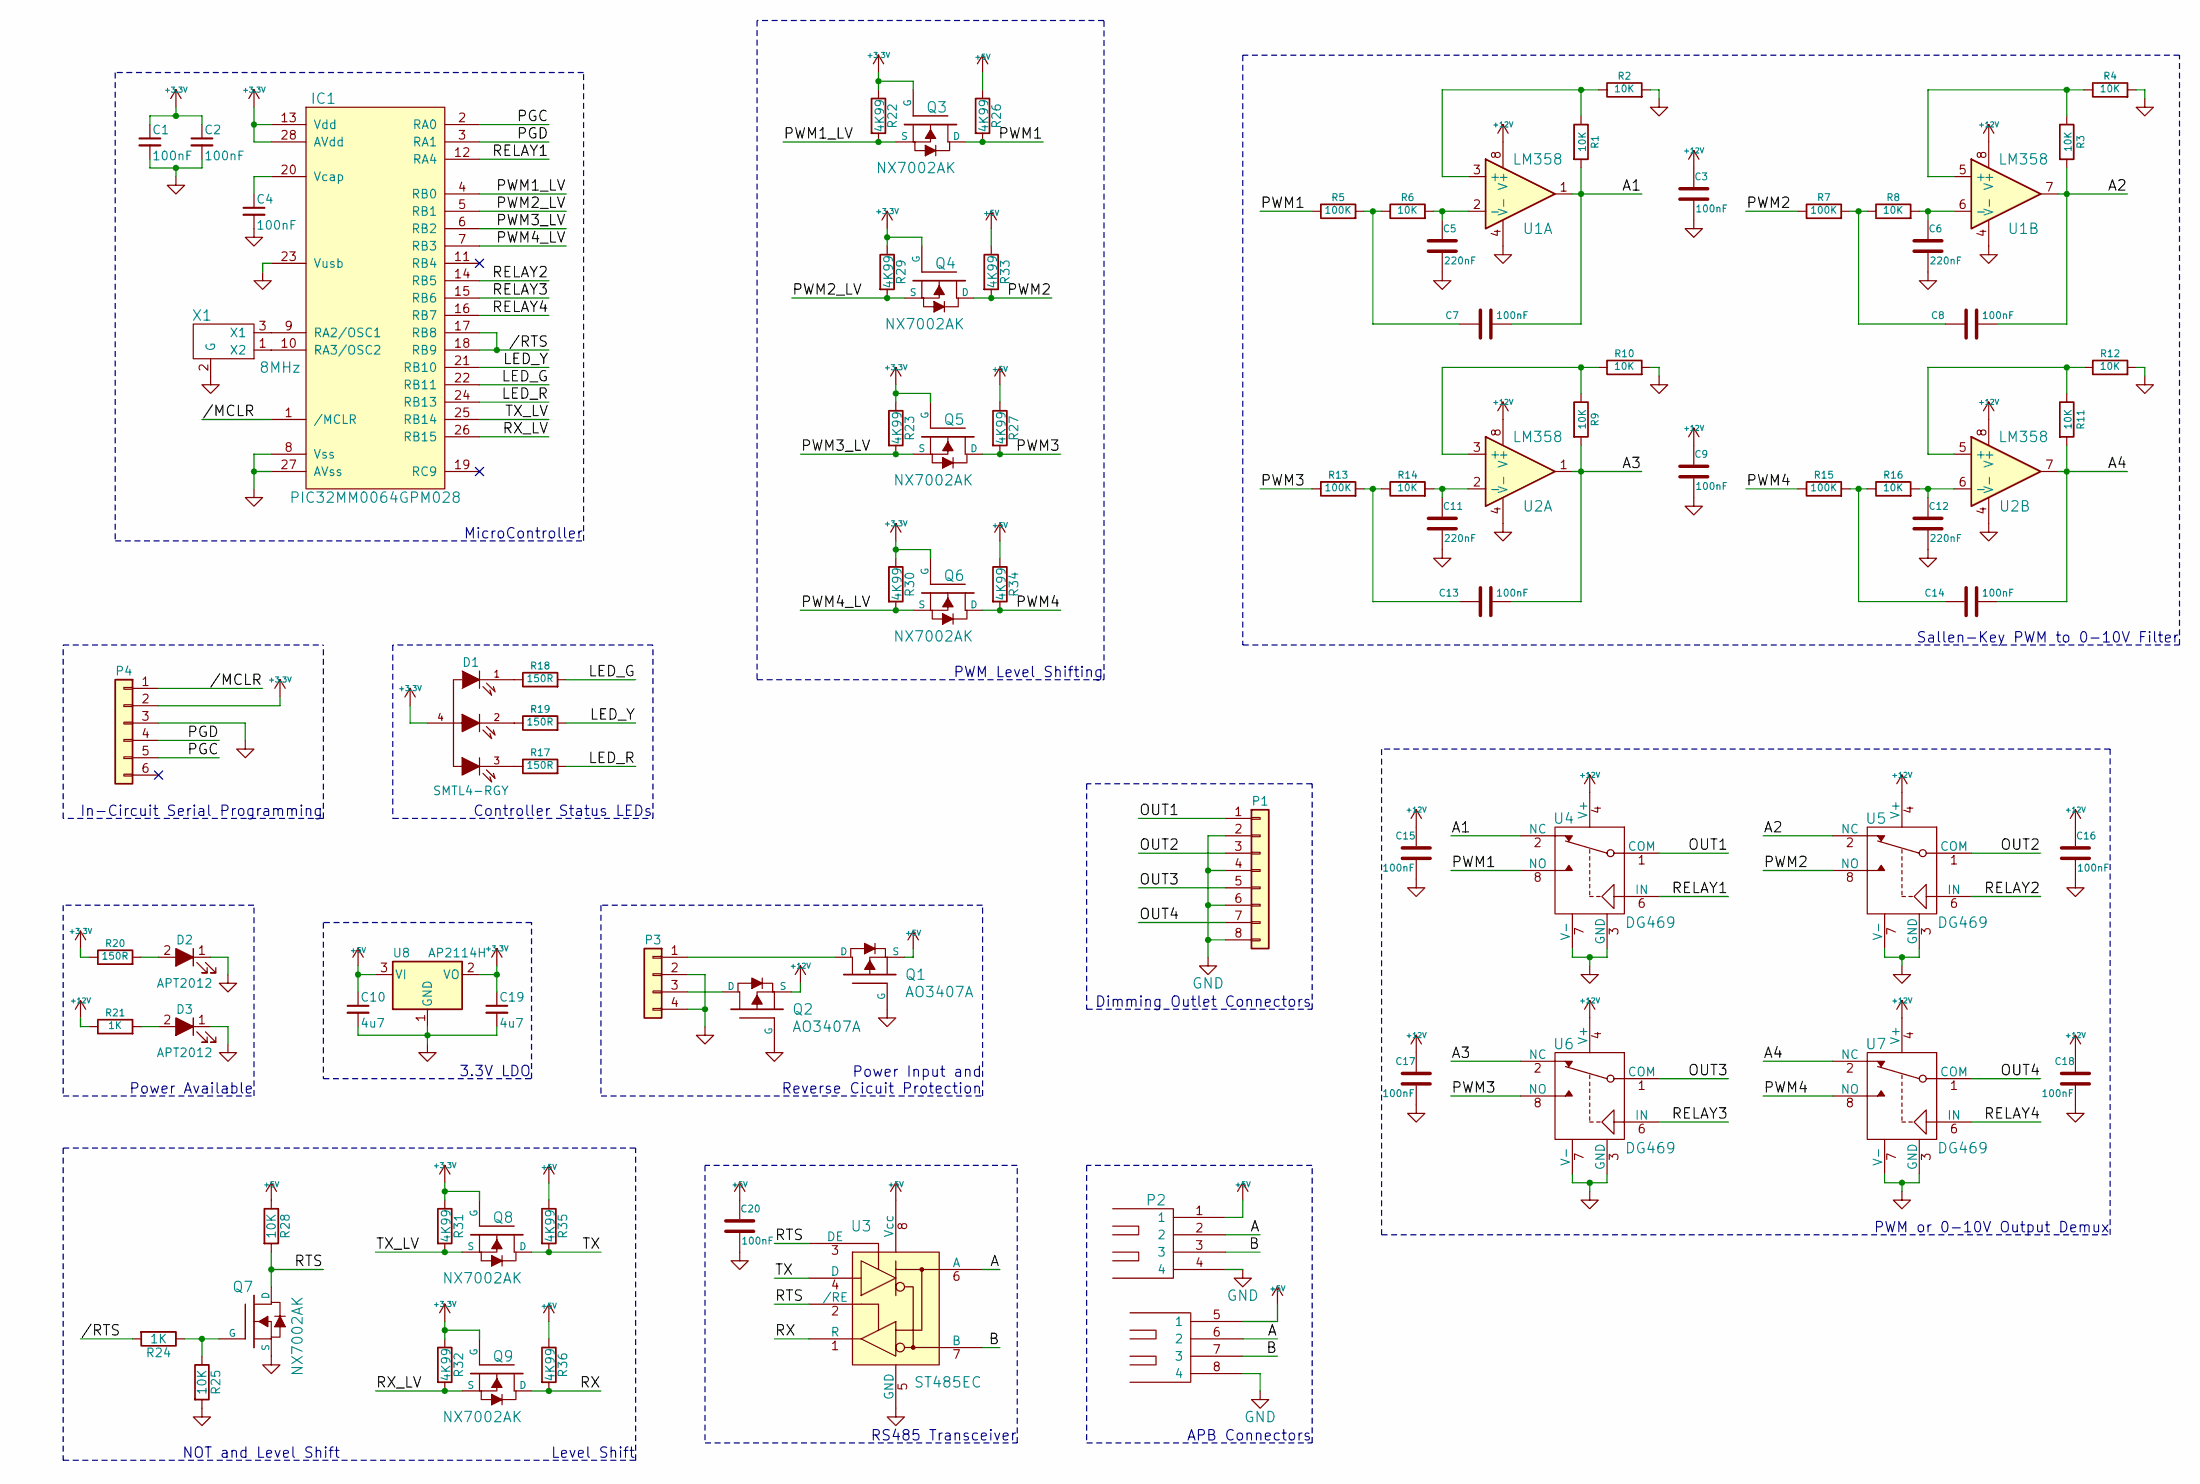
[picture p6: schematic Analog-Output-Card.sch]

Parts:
C1, C2, C3, C4, C7, C8, C9, C13, C14, C15, C16, C17, C18, C20: 100nF; C_0805
C5, C6, C11, C12: 220nF; C_0805
C10, C19: 4u7; C_0805
D1: SMTL4-RGY; PLCC-4
D2, D3: APT2012; LED_0805
IC1: PIC32MM0064GPM028; SSOP-28_5.3x10.2mm_Pitch0.65mm
P1: 1x8 2.54; Screw_Header_1x8
P2: Stacked USBA; USB-1.1_Stacked
P3: 4x1 2.54; Screw_Header_1x4
P4: 2x3 1.27 Pin Header; Pin_Header_Straight_1x06_Pitch2.54mm
Q1, Q2: AO3407A; SOT-23
Q3, Q4, Q5, Q6, Q7, Q8, Q9: NX7002AK; SOT-23
R1, R2, R3, R4, R6, R8, R9, R10, R11, R12, R14, R16, R25, R28: 10K; R_0805
R5, R7, R13, R15: 100K; R_0805
R17, R18, R19, R20: 150R; R_0805
R21, R24: 1K; R_0805
R22, R23, R26, R27, R29, R30, R31, R32, R33, R34, R35, R36: 4K99; R_0805
U1, U2: LM358; TSSOP-8_4.4x3mm_Pitch0.65mm
U3: ST485EC; SOIC-8_3.9x4.9mm_Pitch1.27mm
U4, U5, U6, U7: DG469; TSSOP-8_3x3mm_Pitch0.65mm
U8: AP2114H; SOT-223
X1: 8MHz; Resonator_3.2x1.3

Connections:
+3V3: C1.1, C2.1, C19.1, D1.4, IC1.13 (Vdd), IC1.28 (AVdd), P4.2, Q3.1 (G), Q4.1 (G), Q5.1 (G), Q6.1 (G), Q8.1 (G), Q9.1 (G), R20.1, R22.1, R23.1, R29.1, R30.1, R31.1, R32.1, U8.2 (VO); also elsewhere on the board
+5V: C10.1, C20.1, P2.1, P2.5 (1), Q1.2 (S), R26.1, R27.1, R28.1, R33.1, R34.1, R35.1, R36.1, U3.8 (Vcc), U8.3 (VI)
+12V: C3.1, C9.1, C15.1, C16.1, C17.1, C18.1, Q2.2 (S), R21.1, U1.8 (V+), U2.8 (V+), U4.4 (V+), U5.4 (V+), U6.4 (V+), U7.4 (V+)
//MCLR: IC1.1 (/MCLR), P4.1; also elsewhere on the board
//RTS: IC1.17 (RB8), IC1.18 (RB9), R24.2
/A: P2.2, P2.6 (2), U3.6 (A)
/A1: C7.2, R1.2, U1.1, U4.2 (NC)
/A2: C8.2, R3.2, U1.7, U5.2 (NC)
/A3: C13.2, R9.2, U2.1, U6.2 (NC)
/A4: C14.2, R11.2, U2.7, U7.2 (NC)
/B: P2.3, P2.7 (3), U3.7 (B)
/LED_G: IC1.22 (RB11), R18.2
/LED_R: IC1.24 (RB13), R17.2
/LED_Y: IC1.21 (RB10), R19.2
/OUT1: P1.1, U4.1 (COM)
/OUT2: P1.3, U5.1 (COM)
/OUT3: P1.5, U6.1 (COM)
/OUT4: P1.7, U7.1 (COM)
/PGC: IC1.2 (RA0), P4.5; also elsewhere on the board
/PGD: IC1.3 (RA1), P4.4; also elsewhere on the board
/PWM1: Q3.3 (D), R5.1, R26.2, U4.8 (NO)
/PWM1_LV: IC1.4 (RB0), Q3.2 (S), R22.2
/PWM2: Q4.3 (D), R7.1, R33.2, U5.8 (NO)
/PWM2_LV: IC1.5 (RB1), Q4.2 (S), R29.2
/PWM3: Q5.3 (D), R13.1, R27.2, U6.8 (NO)
/PWM3_LV: IC1.6 (RB2), Q5.2 (S), R23.2
/PWM4: Q6.3 (D), R15.1, R34.2, U7.8 (NO)
/PWM4_LV: IC1.7 (RB3), Q6.2 (S), R30.2
/RELAY1: IC1.12 (RA4), U4.6 (IN)
/RELAY2: IC1.14 (RB5), U5.6 (IN)
/RELAY3: IC1.15 (RB6), U6.6 (IN)
/RELAY4: IC1.16 (RB7), U7.6 (IN)
/RTS: Q7.3 (D), R28.2, U3.2 (/RE), U3.3 (DE)
/RX: Q9.3 (D), R36.2, U3.1 (R)
/RX_LV: IC1.26 (RB15), Q9.2 (S), R32.2
/TX: Q8.3 (D), R35.2, U3.4 (D)
/TX_LV: IC1.25 (RB14), Q8.2 (S), R31.2
GND: C1.2, C2.2, C3.2, C4.2, C5.2, C6.2, C9.2, C10.2, C11.2, C12.2, C15.2, C16.2, C17.2, C18.2, C19.2, C20.2, D2.1 (K), D3.1 (K), IC1.8 (Vss), IC1.23 (Vusb), IC1.27 (AVss), P1.2, P1.4, P1.6, P1.8, P2.4, P2.8 (4), P3.2, P3.4, P4.3, Q1.1 (G), Q2.1 (G), Q7.2 (S), R2.2, R4.2, R10.2, R12.2, R25.2, U1.4 (V-), U2.4 (V-), U3.5 (GND), U4.3 (GND), U4.7 (V-), U5.3 (GND), U5.7 (V-), U6.3 (GND), U6.7 (V-), U7.3 (GND), U7.7 (V-), U8.1 (GND), X1.2 (G); also elsewhere on the board
unnamed: C4.1, IC1.20 (Vcap)
unnamed: C5.1, R6.2, U1.2 (-)
unnamed: C6.1, R8.2, U1.6 (-)
unnamed: C7.1, R5.2, R6.1
unnamed: C8.1, R7.2, R8.1
unnamed: C11.1, R14.2, U2.2 (-)
unnamed: C12.1, R16.2, U2.6 (-)
unnamed: C13.1, R13.2, R14.1
unnamed: C14.1, R15.2, R16.1
unnamed: D1.1, R18.1
unnamed: D1.2, R19.1
unnamed: D1.3, R17.1
unnamed: D2.2 (A), R20.2
unnamed: D3.2 (A), R21.2
unnamed: IC1.9 (RA2/OSC1), X1.3 (X1)
unnamed: IC1.10 (RA3/OSC2), X1.1 (X2)
unnamed: P3.1, Q1.3 (D)
unnamed: P3.3, Q2.3 (D)
unnamed: Q7.1 (G), R24.1, R25.1
unnamed: R1.1, R2.1, U1.3 (+)
unnamed: R3.1, R4.1, U1.5 (+)
unnamed: R9.1, R10.1, U2.3 (+)
unnamed: R11.1, R12.1, U2.5 (+)

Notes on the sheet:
Sallen-Key PWM to 0-10V Filter
PWM or 0-10V Output Demux
Dimming Outlet Connectors
In-Circuit Serial Programming
MicroController
Controller Status LEDs
RS485 Transceiver
APB Connectors
Level Shift
NOT and Level Shift
3.3V LDO
Power Input and Reverse Cicuit Protection
Power Available
PWM Level Shifting

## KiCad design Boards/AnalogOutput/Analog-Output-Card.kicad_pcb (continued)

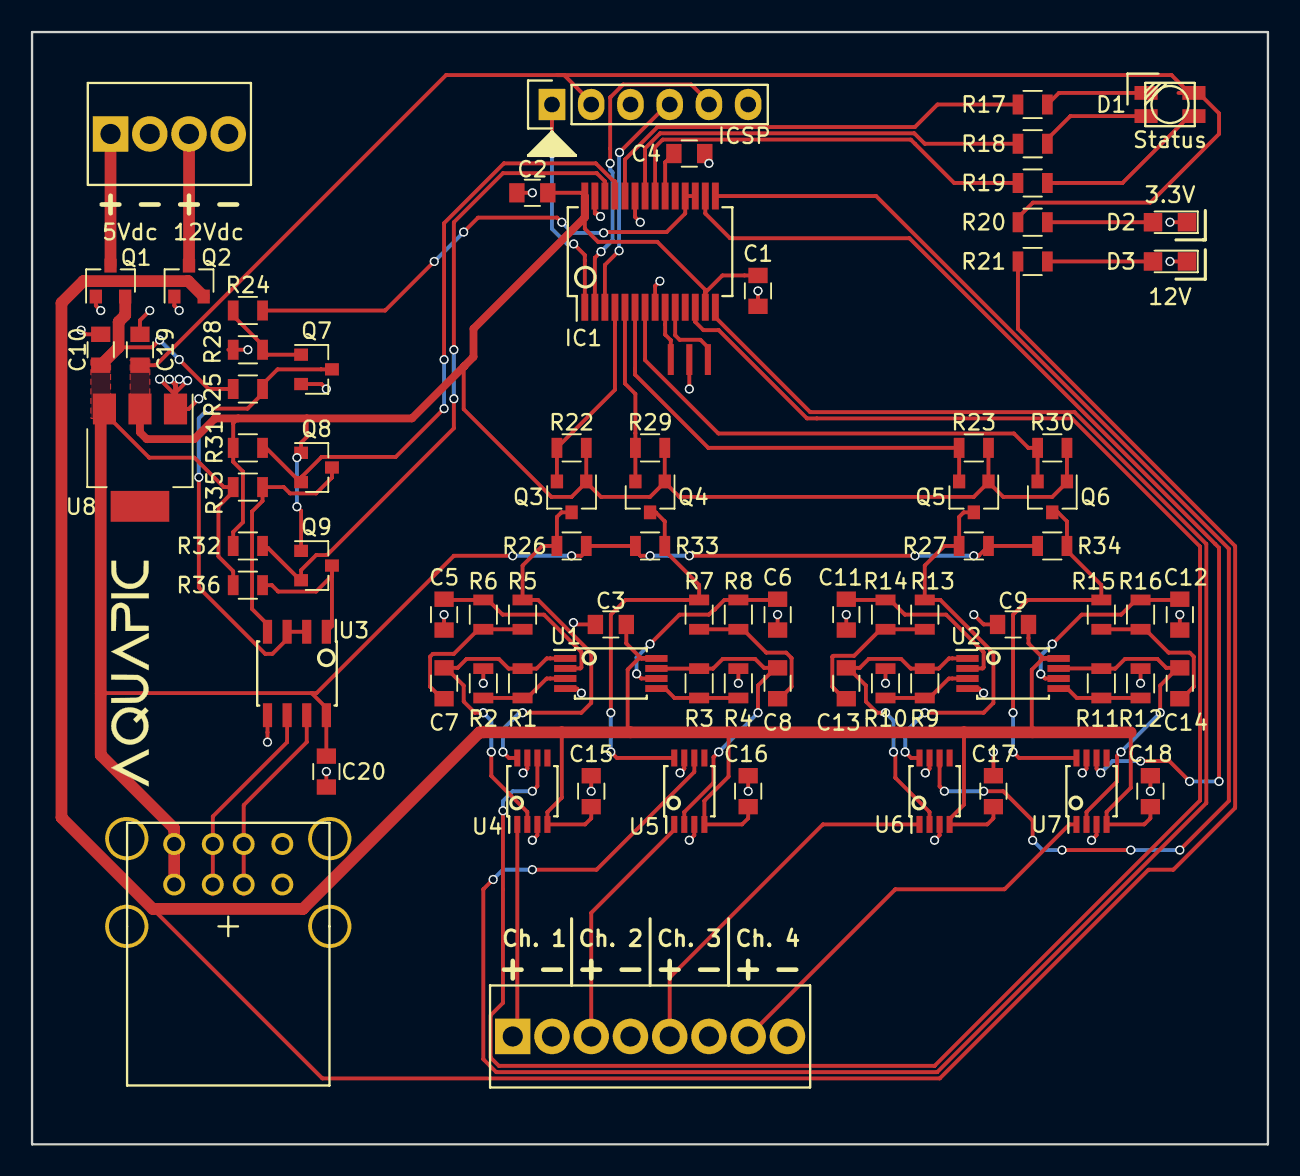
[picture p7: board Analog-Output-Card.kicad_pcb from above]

Board: 2 copper layers, 80.0 x 72.0 mm, 82 parts (0 on the bottom side), 61 nets.

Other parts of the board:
ICSP: 6x1 2.54 Pin Header; Pin_Header_Straight_1x06

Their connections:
+3V3: ICSP.2; also elsewhere on the board
//MCLR: ICSP.1; also elsewhere on the board
/PGC: ICSP.5; also elsewhere on the board
/PGD: ICSP.4; also elsewhere on the board
GND: ICSP.3; also elsewhere on the board

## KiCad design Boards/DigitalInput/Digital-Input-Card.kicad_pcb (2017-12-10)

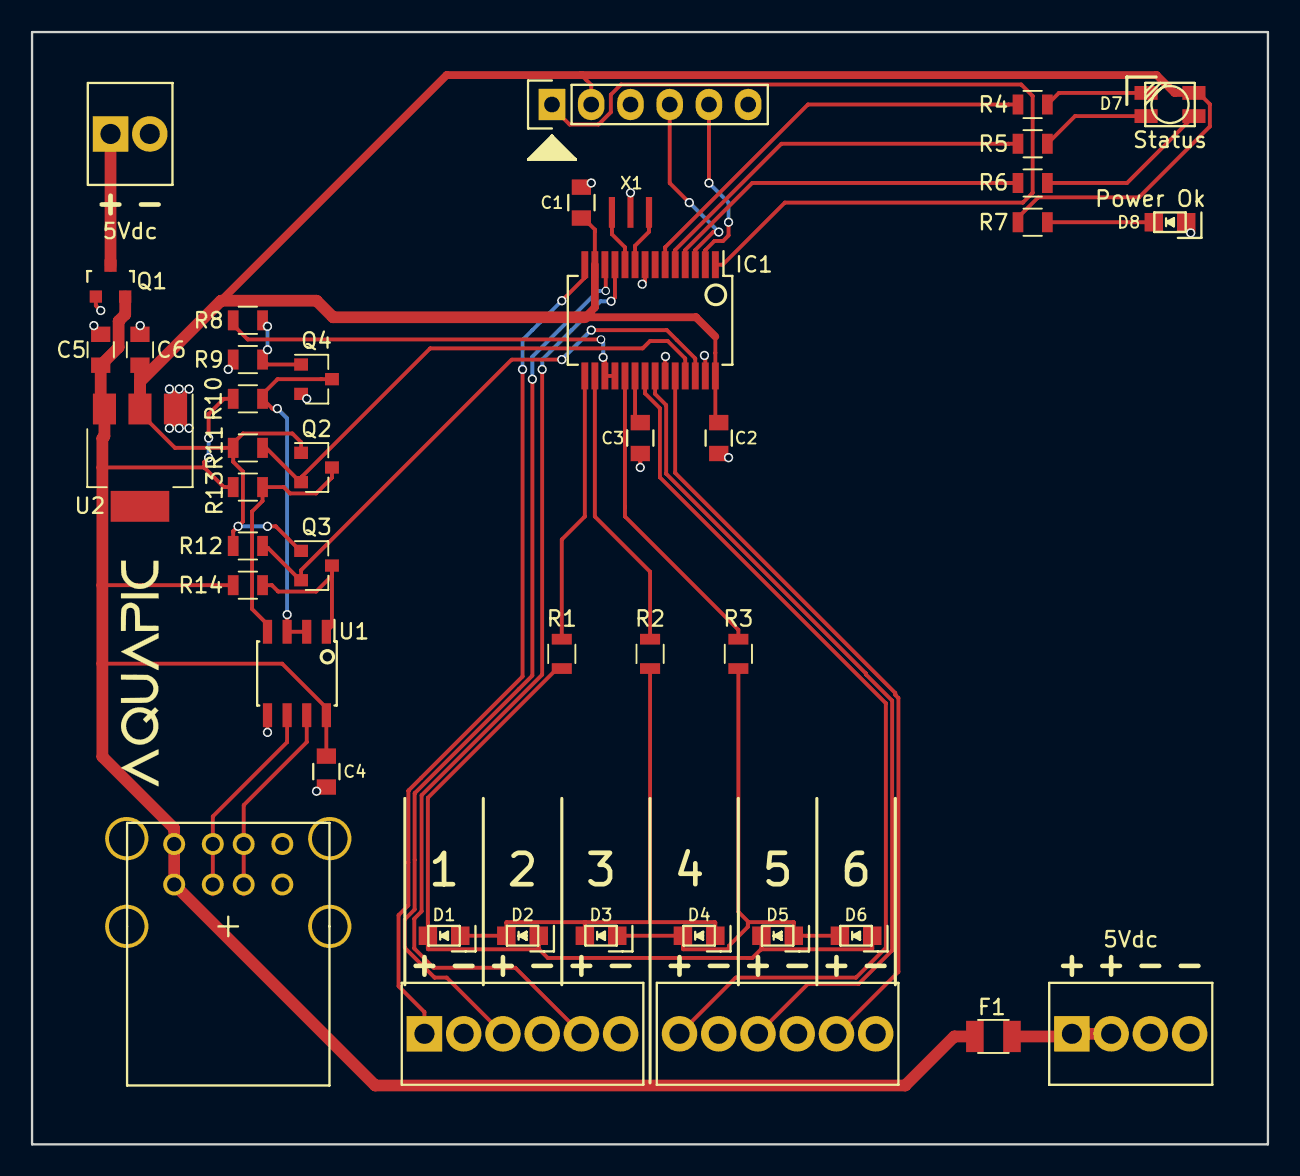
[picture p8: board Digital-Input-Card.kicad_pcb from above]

Board: 2 copper layers, 80.0 x 72.0 mm, 42 parts (0 on the bottom side), 39 nets.

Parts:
C1, C2, C3, C4: 100nF; C_0805
C5, C6: 4u7; C_0805
D1, D2, D3, D4, D5, D6, D8: APT2012; LED-0805
D7: SMTL4-RGY; PLCC-4
F1: 750mA; Fuse_SMD1206_Reflow
IC1: PIC32MM0064GPM028; SSOP-28_5.3x10.2mm_Pitch0.65mm
P1: 1x6 2.54 Pin Header; Pin_Header_Straight_1x06
P2: 1x12 2.54; Screw_Header_1x12
P3: 1x2 2.54; Screw_Header_1x2
P4: 1x4 2.54; Screw_Header_1x4
P5: Stacked USBA; USB-1.1_Stacked
Q1: AO3407A; SOT-23
Q2, Q3, Q4: NX7002AK; SOT-23
R1, R2, R3: 20R; R_0805
R4, R5, R6, R7: 150R; R_0805
R8: 1K; R_0805
R9, R10: 10K; R_0805
R11, R12, R13, R14: 4K99; R_0805
U1: ST485EC; SOIC-8_3.9x4.9mm_Pitch1.27mm
U2: AP2114H; SOT-223
X1: 8MHz; Resonator_3.2x1.3

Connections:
+3V3: C1.1, C2.1, C6.1, D7.4, IC1.13, IC1.28, P1.2, Q2.1, Q3.1, R7.1, R11.1, R12.1, U2.2
+5V: C4.1, C5.1, F1.1, P5.1, P5.5, Q1.2, R10.1, R13.1, R14.1, U1.8, U2.3
//MCLR: IC1.1, P1.1
//RTS: IC1.17, IC1.18, R8.2
/A: P5.2, P5.6, U1.6
/B: P5.3, P5.7, U1.7
/Input1: IC1.14, P2.1
/Input2: IC1.12, P2.3
/Input3: IC1.11, P2.5
/Input4: IC1.21, P2.7
/Input5: IC1.22, P2.9
/Input6: IC1.24, P2.11
/LED1: IC1.15, R1.1
/LED2: IC1.16, R2.1
/LED3: IC1.19, R3.1
/LED_G: IC1.5, R5.2
/LED_R: IC1.6, R4.2
/LED_Y: IC1.4, R6.2
/PGC: IC1.2, P1.5
/PGD: IC1.3, P1.4
/RTS: Q4.3, R10.2, U1.2, U1.3
/RX: Q3.3, R14.2, U1.1
/RX_LV: IC1.26, Q3.2, R12.2
/TX: Q2.3, R13.2, U1.4
/TX_LV: IC1.25, Q2.2, R11.2
GND: C1.2, C2.2, C3.2, C4.2, C5.2, C6.2, D8.1, IC1.8, IC1.23, IC1.27, P1.3, P2.2, P2.4, P2.6, P2.8, P2.10, P2.12, P3.2, P4.3, P4.4, P5.4, P5.8, Q1.1, Q4.2, R9.2, U1.5, U2.1, X1.2
unnamed: C3.1, IC1.20
unnamed: D1.1, D2.2, D3.2, D4.1, R2.2
unnamed: D1.2, D2.1, D5.2, D6.1, R1.2
unnamed: D3.1, D4.2, D5.1, D6.2, R3.2
unnamed: D7.1, R5.1
unnamed: D7.2, R6.1
unnamed: D7.3, R4.1
unnamed: D8.2, R7.2
unnamed: F1.2, P4.1, P4.2
unnamed: IC1.9, X1.3
unnamed: IC1.10, X1.1
unnamed: P3.1, Q1.3
unnamed: Q4.1, R8.1, R9.1

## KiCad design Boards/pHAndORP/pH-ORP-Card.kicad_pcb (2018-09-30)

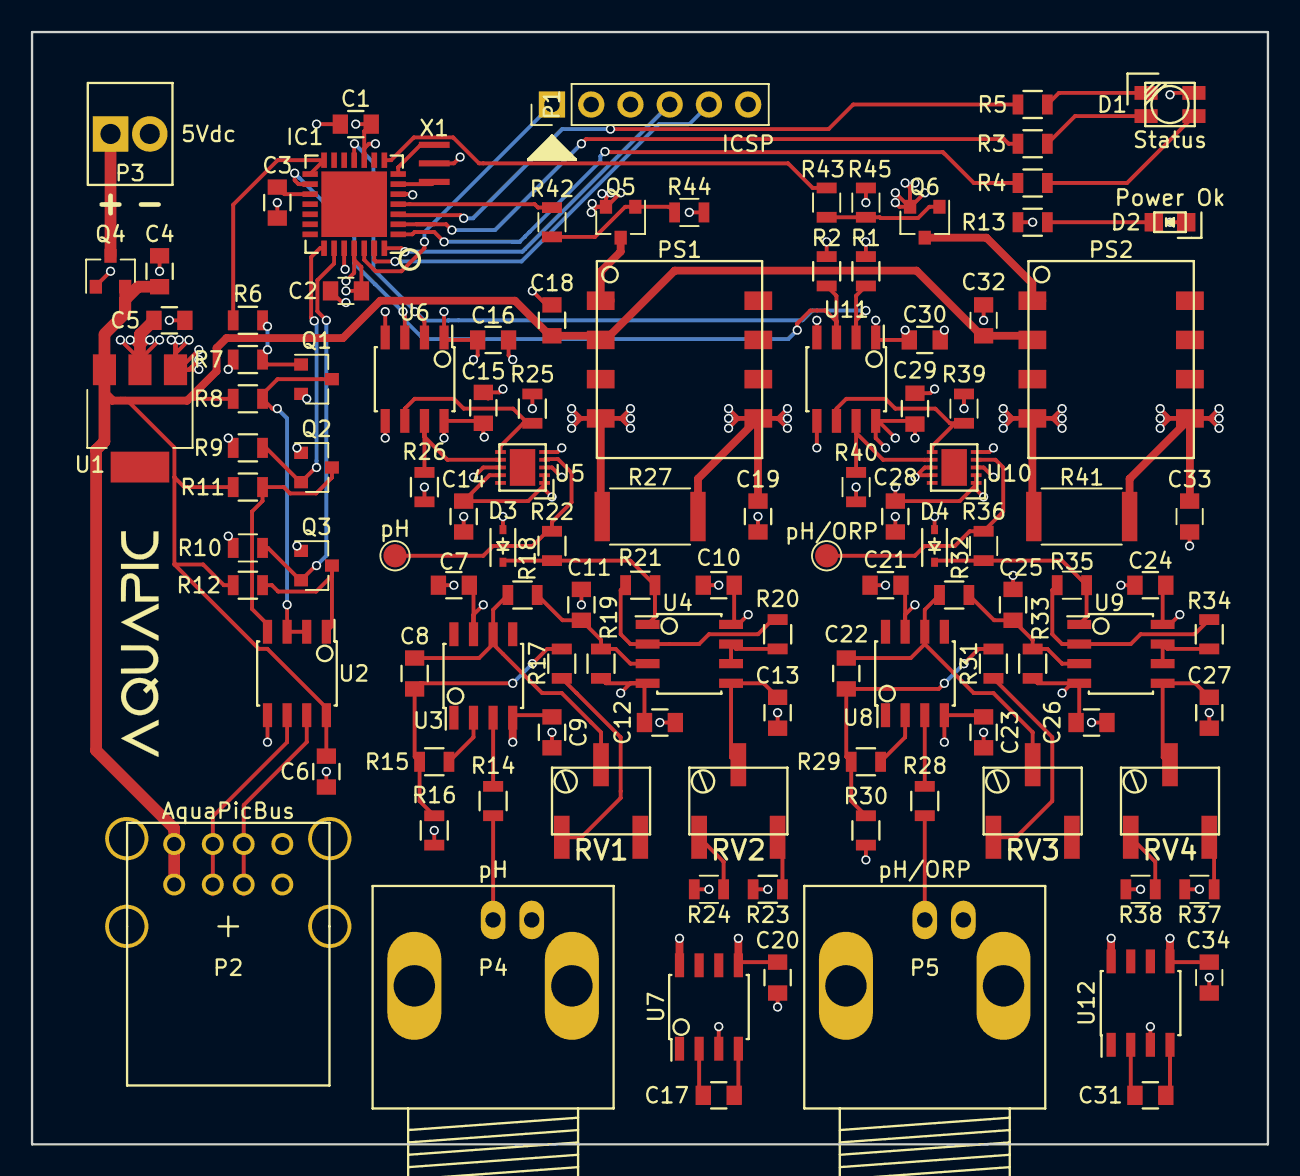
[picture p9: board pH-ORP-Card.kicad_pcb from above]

Board: 4 copper layers, 80.0 x 72.0 mm, 116 parts (0 on the bottom side), 76 nets.

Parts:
C1, C2, C3, C6, C7, C9, C10, C11, C12, C14, C15, C16, C21, C23, C24, C25, C26, C28, C29, C30: 100nF; C_0805
C4, C5, C18, C32: 4u7; C_0805
C8, C22: 33pF; C_0805
C13, C27: 1uF; C_0805
C17, C19, C20, C31, C33, C34: 10uF; C_0805
D1: SMTL4-RGY; PLCC-4
D2: APT2012; LED-0805
D3, D4: DB2J310; SOD-323
IC1: PIC32MM0064GPM028; QFN-28-1EP_6x6mm_Pitch0.65mm
P1: ICSP; PinHeader_1x06_P2.54mm_Vertical
P2: AquaPicBus; USB-1.1_Stacked
P3: 5Vdc; Screw_Header_1x2
P4: pH; BNC_Socket_TYCO-AMP_LargePads
P5: pH/ORP; BNC_Socket_TYCO-AMP_LargePads
PS1, PS2: R1SE-0505; 8-SMD
Q1, Q2, Q3, Q5, Q6: NX7002AK; SOT-23
Q4: AO3407A; SOT-23
R1, R2, R9, R10, R11, R12, R25, R26, R39, R40: 4K99; R_0805
R3, R4, R5, R13: 150R; R_0805
R6, R22, R36, R42, R43: 1K; R_0805
R7, R8, R14, R23, R24, R28, R37, R38, R44, R45: 10K; R_0805
R15, R29: 2M; R_0805
R16: 49K9; R_0805
R17, R18, R19, R20, R21, R31, R32, R33, R34, R35: 221K; R_0805
R27, R41: 50R; R_2512
R30: 100K; R_0805
RV1, RV3: 50K; POTENTIAMETER_SMD
RV2, RV4: 10K; POTENTIAMETER_SMD
TP1: pH; TestPoint_Pad_D1.5mm
TP2: pH/ORP; TestPoint_Pad_D1.5mm
U1: AP2114H; SOT-223
U2: ST485EC; SOIC-8_3.9x4.9mm_Pitch1.27mm
U3, U8: LMC6061; SOIC-8_3.9x4.9mm_Pitch1.27mm
U4, U9: TLV272; SOIC-8_3.9x4.9mm_Pitch1.27mm
U5, U10: LTC2483; DFN-10_3x3mm
U6, U11: Si8602; SOIC-8_3.9x4.9mm_Pitch1.27mm
U7, U12: TC7660; SOIC-8_3.9x4.9mm_Pitch1.27mm
X1: 8MHz; Resonator_3.2x1.3

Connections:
+3V3: C1.1, C2.1, C5.1, C16.1, C30.1, D1.4, IC1.10, IC1.25, P1.2, Q2.1, Q3.1, R1.1, R2.1, R9.1, R10.1, R13.1, U1.2, U6.1, U11.1
+5V: C4.1, C6.1, C18.1, C32.1, P2.1, P2.5, PS1.2, PS2.2, Q4.2, R8.1, R11.1, R12.1, U1.3, U2.8
+5VA: C21.1, C24.1, C28.1, C29.1, C33.1, PS2.5, R39.1, R40.1, R41.1, U8.7, U9.8, U10.1, U10.2, U11.8, U12.8
+5VD: C7.1, C10.1, C14.1, C15.1, C19.1, PS1.5, R25.1, R26.1, R27.1, U3.7, U4.8, U5.1, U5.2, U5.9, U6.8, U7.8
-5V: C9.2, C11.2, C12.2, C20.2, R19.2, R24.2, U3.4, U4.4, U7.5
-5VA: C23.2, C25.2, C26.2, C34.2, R33.2, R38.2, U8.4, U9.4, U12.5
//MCLR: IC1.26, P1.1
//RTS: IC1.14, IC1.15, R6.2
/A: P2.2, P2.6, U2.6
/A_pH: R22.2, TP1.1, U5.4
/A_pH/ORP: R36.2, TP2.1, U10.4
/B: P2.3, P2.7, U2.7
/En_pH: IC1.4, R42.2
/En_pH/ORP: IC1.8, R43.2
/LED_G: IC1.2, R3.2
/LED_R: IC1.3, R5.2
/LED_Y: IC1.1, R4.2
/PGC: IC1.27, P1.5
/PGD: IC1.28, P1.4
/RTS: Q1.3, R8.2, U2.2, U2.3
/RX: Q3.3, R12.2, U2.1
/RX_LV: IC1.23, Q3.2, R10.2
/SCL: IC1.16, R2.2, U6.3, U11.3
/SDA: IC1.11, R1.2, U6.2, U11.2
/TX: Q2.3, R11.2, U2.4
/TX_LV: IC1.22, Q2.2, R9.2
GND: C1.2, C2.2, C3.2, C4.2, C5.2, C6.2, C16.2, C18.2, C30.2, C32.2, D2.1, IC1.5, IC1.24, P1.3, P2.4, P2.8, P3.2, Q1.2, Q4.1, Q5.2, Q6.2, R7.2, R44.2, R45.2, U1.1, U2.5, U6.4, U11.4, X1.2
GNDA: C21.2, C23.1, C24.2, C26.1, C27.1, C28.2, C29.2, C33.2, C34.1, D4.2, P5.2, PS2.4, R30.2, R37.1, R41.2, U10.3, U10.5, U10.8, U10.9, U11.5, U12.3
GNDD: C7.2, C9.1, C10.2, C12.1, C13.1, C14.2, C15.2, C19.2, C20.1, D3.2, P4.2, PS1.4, R16.2, R23.1, R27.2, U5.3, U5.5, U5.8, U6.5, U7.3
unnamed: C3.1, IC1.17
unnamed: C8.1, R15.2, R16.1, R17.1
unnamed: C8.2, R18.1, RV1.2, U3.6
unnamed: C11.1, R18.2, R19.1, U4.3
unnamed: C13.2, RV2.2, U4.5
unnamed: C17.1, U7.2
unnamed: C17.2, U7.4
unnamed: PS1.1, Q5.3
unnamed: C22.1, R29.2, R30.1, R31.1
unnamed: C22.2, R32.1, RV3.2, U8.6
unnamed: C25.1, R32.2, R33.1, U9.3
unnamed: C27.2, RV4.2, U9.5
unnamed: C31.1, U12.2
unnamed: C31.2, U12.4
unnamed: PS2.1, Q6.3
unnamed: D1.1, R3.1
unnamed: D1.2, R4.1
unnamed: D1.3, R5.1
unnamed: D2.2, R13.2
unnamed: D3.1, R21.2, R22.1, U4.1
unnamed: D4.1, R35.2, R36.1, U9.1
unnamed: IC1.6, X1.3
unnamed: IC1.7, X1.1
unnamed: P3.1, Q4.3
unnamed: P4.1, R14.1
unnamed: P5.1, R28.1
unnamed: Q1.1, R6.1, R7.1
unnamed: Q5.1, R42.1, R44.1
unnamed: Q6.1, R43.1, R45.1
unnamed: R14.2, U3.3
unnamed: R15.1, U3.2
unnamed: R17.2, RV1.1
unnamed: R20.1, R21.1, U4.2
unnamed: R20.2, U4.6, U4.7
unnamed: R23.2, RV2.3
unnamed: R24.1, RV2.1
unnamed: R25.2, U5.6, U6.6
unnamed: R26.2, U5.7, U6.7
unnamed: R28.2, U8.3
unnamed: R29.1, U8.2
unnamed: R31.2, RV3.1
unnamed: R34.1, R35.1, U9.2
unnamed: R34.2, U9.6, U9.7
unnamed: R37.2, RV4.3
unnamed: R38.1, RV4.1
unnamed: R39.2, U10.6, U11.6
unnamed: R40.2, U10.7, U11.7

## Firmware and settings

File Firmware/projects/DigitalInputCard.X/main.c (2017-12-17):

/*******************************************************************************
 * pH ORP Card - main.c
 *
 * Goodtime Development 
 * 
 * Created 2017 Skyler Brandt
 *
 * Description:
 *  Firmware for the analog input card
 * 
 * Device:
 *  PIC32MM0064GPM028
 ******************************************************************************/

/******************************************************************************/
/* License                                                                    */
/******************************************************************************/
/*******************************************************************************
 * Copyright (c) 2017 Goodtime Development
 *
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
 * You should have received a copy of the GNU General Public License
 * along with this program.  If not, see http://www.gnu.org/licenses/
 ******************************************************************************/

#include "mcc_generated_files/mcc.h"
#include "../../lib/aquaPicBus/aquaPicBus.h"

/******************************************************************************/
/* Defines                                                                    */
/******************************************************************************/
/* General Outputs and Inputs */
/* Red LED is RB0 */
#define RED_LED(state)      state ? N_R_LED_SetLow() : N_R_LED_SetHigh()
/* Green LED is RB1 */
#define GREEN_LED(state)    state ? N_G_LED_SetLow() : N_G_LED_SetHigh()
/* Yellow LED is RB2 */
#define YELLOW_LED(state)   state ? N_Y_LED_SetLow() : N_Y_LED_SetHigh()
#define ON                  1
#define OFF                 0

/* AquaPic Bus Settings */
#define APB_ADDRESS         0x30
#define FRAMING_TIMER       1   /* Framing called from timer 1 at 1mSec */
#define ERROR_TIME          10  /* 10 sec alarm   */

/* Digital Inputs */
#define NUM_INPUTS          6
#define DECOUNCE_LIMIT      25 
#define DEBOUNCE_INIT       128
#define ALL_LEDS_OFF        255

/******************************************************************************/
/* Functions                                                                  */
/******************************************************************************/
void apbMessageHandler(uint8_t function, uint8_t* message, uint8_t messageLength);
void putsch(uint8_t* data, uint8_t length);
uint32_t readInputValue(uint8_t input);
void turnOnInputLed(uint8_t led);

/******************************************************************************/
/* Variable Definitions                                                       */
/******************************************************************************/
typedef enum inputStateEnum {
    OPEN = 0,
    CLOSE = 1
}inputState_t;

struct inputObjStruct {
    inputState_t state;
    uint8_t debounceTime;
};

/******************************************************************************/
/* Variables                                                                  */
/******************************************************************************/
struct inputObjStruct inputs[NUM_INPUTS];
uint8_t ledIndex;
int8_t apbLastErrorState;
uint8_t i;

void main(void) {
    /* initialize the device */
    SYSTEM_Initialize();

    /* AquaPic Bus initialization */
    if (!apb_init(&apbMessageHandler, 
            &putsch,
            APB_ADDRESS,
            FRAMING_TIMER,
            ERROR_TIME)) {
        while (1);
    }
    apbLastErrorState = 0;
    
    /* Input initialization */
    for (i = 0; i < NUM_INPUTS; ++i) {
        inputs[i].state = OPEN;
        inputs[i].debounceTime = DEBOUNCE_INIT;
    }
    ledIndex = 0;
    
    /* Enable the Global Interrupts */
    INTERRUPT_GlobalEnable();
    /* Start the timer */
    TMR1_Start();
    
    YELLOW_LED(OFF);
    GREEN_LED(ON);
    
    while (1) {
        while (!UART1_ReceiveBufferIsEmpty()) {
            apb_run(UART1_Read());
        }
        
        int8_t apbError = apb_isErrored();
        if (apbError && !apbLastErrorState) {
            GREEN_LED(OFF);
            RED_LED(ON);
        } else if (!apbError && apbLastErrorState) {
            RED_LED(OFF);
            GREEN_LED(ON);
        }
        apbLastErrorState = apbError;
    }
}

void apbMessageHandler(uint8_t function, uint8_t* message, uint8_t messageLength) {
    switch (function) {
        case 10: { /* read single channel value */
            uint8_t channel = message[3];
            uint8_t value = 0;
            if (channel >= 0)
            if (channel < NUM_INPUTS) {
                value = (uint8_t)inputs[channel].state;
            }
            
            apb_initResponse();
            apb_appendToResponse(value);
            apb_sendResponse();
            break;
        }
        case 20: { /* read all channels values */
            uint8_t values = 0x00;            
            int i;
            for (i = 0; i < NUM_INPUTS; ++i) {
                values |= (uint8_t)inputs[i].state << i;
            }

            apb_initResponse();
            apb_appendToResponse(values);
            apb_sendResponse();
            break;
        }
        default:
            break;
    }
}

void putsch(uint8_t* data, uint8_t length) {
    UART1_WriteBuffer(data, length);
}

/* Defined in tmr1.h */
void TMR1_CallBack() {
    /* AquaPic Bus framing */
    apb_framing();
    
    /* Debounce inputs */
    for (i = 0; i < NUM_INPUTS; ++i) {
        /* Inputs are active low */
        if (!readInputValue(i)) {
            inputs[i].debounceTime++;
            if (inputs[i].debounceTime > (DEBOUNCE_INIT + DECOUNCE_LIMIT)) {
                inputs[i].debounceTime = DEBOUNCE_INIT + DECOUNCE_LIMIT;
                inputs[i].state = CLOSE;
            }
        } else {
            inputs[i].debounceTime--;
            if (inputs[i].debounceTime < (DEBOUNCE_INIT - DECOUNCE_LIMIT)) {
                inputs[i].debounceTime = DEBOUNCE_INIT - DECOUNCE_LIMIT;
                inputs[i].state = OPEN;
            }
        }
    }
    
    /* Multiplex LEDs */
    inputs[i].state ? turnOnInputLed(ledIndex) : turnOnInputLed(ALL_LEDS_OFF);
    ledIndex = ++ledIndex % NUM_INPUTS;
}

uint32_t readInputValue(uint8_t input) {
    uint32_t value;
    switch(input) {
        case 0:
            value = INPUT_1_GetValue();
            break;
        case 1:
            value = INPUT_2_GetValue();
            break;
        case 2:
            value = INPUT_3_GetValue();
            break;
        case 3:
            value = INPUT_4_GetValue();
            break;
        case 4:
            value = INPUT_5_GetValue();
            break;
        case 5:
            value = INPUT_6_GetValue();
            break;
        default:
            /* Inputs are active low */
            value = 1;
            break;
    }
    return value;
}

void turnOnInputLed(uint8_t led) {
    switch(led) {
        case 0:
            /* Disable line 3 */
            LED_3_SetDigitalInput();
            /* Enable lines 1 and 2 */
            LED_1_SetDigitalOutput();
            LED_2_SetDigitalOutput();
            /* Line 1 high, line 2 low */
            LED_1_SetHigh();
            LED_2_SetLow();
            break;
        case 1:
            /* Disable line 3 */
            LED_3_SetDigitalInput();
            /* Enable lines 1 and 2 */
            LED_1_SetDigitalOutput();
            LED_2_SetDigitalOutput();
            /* Line 2 high, line 1 low */
            LED_2_SetHigh();
            LED_1_SetLow();
            break;
        case 2:
            /* Disable line 1 */
            LED_1_SetDigitalInput();
            /* Enable lines 2 and 3 */
            LED_2_SetDigitalOutput();
            LED_3_SetDigitalOutput();
            /* Line 2 high, line 3 low */
            LED_2_SetHigh();
            LED_3_SetLow();
            break;
        case 3:
            /* Disable line 1 */
            LED_1_SetDigitalInput();
            /* Enable lines 2 and 3 */
            LED_2_SetDigitalOutput();
            LED_3_SetDigitalOutput();
            /* Line 3 high, line 2 low */
            LED_3_SetHigh();
            LED_2_SetLow();
            break;
        case 4:
            /* Disable line 2 */
            LED_2_SetDigitalInput();
            /* Enable lines 1 and 3 */
            LED_1_SetDigitalOutput();
            LED_3_SetDigitalOutput();
            /* Line 1 high, line 3 low */
            LED_1_SetHigh();
            LED_3_SetLow();
            break;
        case 5:
            /* Disable line 2 */
            LED_2_SetDigitalInput();
            /* Enable lines 1 and 3 */
            LED_1_SetDigitalOutput();
            LED_3_SetDigitalOutput();
            /* Line 3 high, line 1 low */
            LED_3_SetHigh();
            LED_1_SetLow();
            break;
        /* turn everything off */
        default:
            LED_1_SetDigitalInput();
            LED_2_SetDigitalInput();
            LED_3_SetDigitalInput();
            break;
    }
}

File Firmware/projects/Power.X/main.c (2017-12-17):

/*******************************************************************************
 * Power - main.c
 *
 * Goodtime Development 
 * 
 * Created 2017 Skyler Brandt
 *
 * Description:
 *  Firmware for the power strip
 * 
 * Device:
 *  PIC32MM0064GPM028
 ******************************************************************************/

/******************************************************************************/
/* License                                                                    */
/******************************************************************************/
/*******************************************************************************
 * Copyright (c) 2017 Goodtime Development
 *
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
 * You should have received a copy of the GNU General Public License
 * along with this program.  If not, see http://www.gnu.org/licenses/
 ******************************************************************************/

#include "mcc_generated_files/mcc.h"
#include "../../lib/aquaPicBus/aquaPicBus.h"
#include "../../lib/PIC32MM/nvm/nvm.h"
#include "../../lib/common/common.h"

/******************************************************************************/
/* Defines                                                                    */
/******************************************************************************/
/* General Outputs and Inputs */
/* Red LED is RB0 */
#define RED_LED(state)      state ? N_R_LED_SetLow() : N_R_LED_SetHigh()
/* Green LED is RB1 */
#define GREEN_LED(state)    state ? N_G_LED_SetLow() : N_G_LED_SetHigh()
/* Yellow LED is RB2 */
#define YELLOW_LED(state)   state ? N_Y_LED_SetLow() : N_Y_LED_SetHigh()
#define ON                  1
#define OFF                 0

/* AquaPic Bus Settings */
#define APB_ADDRESS         0x10
#define FRAMING_TIMER       1   /* Framing called from timer 1 at 1mSec */
#define ERROR_TIME          10  /* 10 sec alarm   */

/* Application */
#define NUM_OUTLETS         8
//#define ENABLE_CURRENT      
#define LPF_FACTOR          5

/******************************************************************************/
/* Functions                                                                  */
/******************************************************************************/
void apbMessageHandler(uint8_t function, uint8_t* message, uint8_t messageLength);
void putsch(uint8_t* data, uint8_t length);
void setOutletState(uint8_t input, uint8_t state);
uint8_t getOutletStates();

/******************************************************************************/
/* Variables                                                                  */
/******************************************************************************/
int8_t apbLastErrorState;
uint8_t fallbackFlags;
int16_t currents[NUM_OUTLETS];
uint8_t i;

void main(void) {
    /* initialize the device */
    SYSTEM_Initialize();
    
    /* AquaPic Bus initialization */
    if (!apb_init(&apbMessageHandler, 
            &putsch,
            APB_ADDRESS,
            FRAMING_TIMER,
            ERROR_TIME)) {
        while (1);
    }
    apbLastErrorState = 0;
    
    /* Read fallback flags from memory */
    fallbackFlags = (uint8_t)nvm_read(0);

#ifdef ENABLE_CURRENT
    for (i = 0; i < NUM_OUTLETS; ++i) {
        currents[i] = 0;
    }
    
    /* Start the ADC */
    AD1CON1SET = 1 << _AD1CON1_ON_POSITION;
    AD1CON1SET = 1 << _AD1CON1_SAMP_POSITION;
    /* Clear the interrupt flag */
    IFS1CLR = 1 << _IFS1_AD1IF_POSITION;
#endif
    
    /* Enable the Global Interrupts */
    INTERRUPT_GlobalEnable();
    
    /* Start timer 1 */
    TMR1_Start();
    
    YELLOW_LED(OFF);
    GREEN_LED(ON);
    
    while (1) {
        while (!UART1_ReceiveBufferIsEmpty()) {
            apb_run(UART1_Read());
        }
        
#ifdef ENABLE_CURRENT
        /* The conversion scan is complete */
        if (IFS1bits.AD1IF) {
            uint16_t results[NUM_OUTLETS];
            /* Clear the interrupt flag */
            IFS1CLR = 1 << _IFS1_AD1IF_POSITION;
            /* Get the results from ADC buffers */
            ADC1_ConversionResultBufferGet(results);
            /* Filter results */
            for (i = 0; i < NUM_OUTLETS; ++i) {
                currents[i] = LPF_FACTOR * currents[i] + results[i];
                currents[i] /= LPF_FACTOR + 1;
            }
        }
#endif 
        
        int8_t apbError = apb_isErrored();
        /* Error rising edge */
        if (apbError && !apbLastErrorState) {
            /* Set outlets to fallback state */
            for (i = 0; i < NUM_OUTLETS; ++i) {
                setOutletState(i, testFlagBit(fallbackFlags, i));
            }
            /* Show red led */
            GREEN_LED(OFF);
            RED_LED(ON);
        /* Error falling edge */
        } else if (!apbError && apbLastErrorState) {
            /*  */
            RED_LED(OFF);
            GREEN_LED(ON);
        }
        /* Store error value */
        apbLastErrorState = apbError;
    }
}

void apbMessageHandler(uint8_t function, uint8_t* message, uint8_t messageLength) {
    switch (function) {
        case 2: { /* setup single channel */
            uint8_t oldFallbackFlags = fallbackFlags;
            assignFlagStateBit(fallbackFlags, message[3], message[4]);
            /* only write to flash if different */
            if (oldFallbackFlags != fallbackFlags) {
                nvm_write(0, fallbackFlags);
            }
            apb_sendDefualtResponse();
            break;
        }
#ifdef ENABLE_CURRENT
        case 10: { /* read outlet current */
            uint8_t outlet = message[3];
            uint16_t current = currents[outlet];
            apb_initResponse();
            apb_appendToResponse(outlet);
            apb_addToResponse(&current, sizeof(uint16_t));
            apb_sendResponse();
            break;
        }
#endif
        case 20: { /* read status */
            apb_initResponse();
            AC_AVAIL_GetValue() ? apb_appendToResponse(0xFF) : apb_appendToResponse(0x00);
            apb_appendToResponse(getOutletStates());
#ifdef ENABLE_CURRENT
            apb_appendToResponse(0xFF);
#else
            apb_appendToResponse(0x00);
#endif
            apb_sendResponse();
            break;
        }
#ifdef ENABLE_CURRENT
        case 21: { /* read all current */
            int i;
            apb_initResponse();
            apb_addToResponse(&(currents[i]), sizeof(uint16_t) * NUM_OUTLETS);
            apb_sendResponse();
            break;
        }
#endif
        case 30: { /* write outlet */
            setOutletState(message[3], message[4]);
            apb_sendDefualtResponse();
            break;
        }
        default:
            break;
    }
}

void putsch(uint8_t* data, uint8_t length) {
    UART1_WriteBuffer(data, length);
}
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

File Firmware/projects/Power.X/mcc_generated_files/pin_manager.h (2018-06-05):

/**
  System Interrupts Generated Driver File

  @Company:
    Microchip Technology Inc.

  @File Name:
    pin_manager.h

  @Summary:
    This is the generated manager file for the MPLAB(c) Code Configurator device.  This manager
    configures the pins direction, initial state, analog setting.
    The peripheral pin select, PPS, configuration is also handled by this manager.

  @Description:
    This source file provides implementations for MPLAB(c) Code Configurator interrupts.
    Generation Information :
        Product Revision  :  MPLAB(c) Code Configurator - 4.26.2
        Device            :  PIC32MM0064GPM048
    The generated drivers are tested against the following:
        Compiler          :  XC32 1.42
        MPLAB             :  MPLAB X 3.60

    Copyright (c) 2013 - 2015 released Microchip Technology Inc.  All rights reserved.

    Microchip licenses to you the right to use, modify, copy and distribute
    Software only when embedded on a Microchip microcontroller or digital signal
    controller that is integrated into your product or third party product
    (pursuant to the sublicense terms in the accompanying license agreement).

    You should refer to the license agreement accompanying this Software for
    additional information regarding your rights and obligations.

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
*/

#ifndef _PIN_MANAGER_H
#define _PIN_MANAGER_H
/**
    Section: Includes
*/
#include <xc.h>
/**
    Section: Device Pin Macros
*/
/**
  @Summary
    Sets the GPIO pin, RA0, high using LATAbits.LATA0.

  @Description
    Sets the GPIO pin, RA0, high using LATAbits.LATA0.

  @Preconditions
    The RA0 must be set to an output.

  @Returns
    None.

  @Param
    None.

  @Example
    <code>
    // Set RA0 high (1)
    CURRENT_5_SetHigh();
    </code>

*/
#define CURRENT_5_SetHigh()          ( LATASET = (1 << 0) )
/**
  @Summary
    Sets the GPIO pin, RA0, low using LATAbits.LATA0.

  @Description
    Sets the GPIO pin, RA0, low using LATAbits.LATA0.

  @Preconditions
    The RA0 must be set to an output.

  @Returns
    None.

  @Param
    None.

  @Example
    <code>
    // Set RA0 low (0)
    CURRENT_5_SetLow();
    </code>

*/
#define CURRENT_5_SetLow()           ( LATACLR = (1 << 0) )
/**
  @Summary
    Toggles the GPIO pin, RA0, using LATAbits.LATA0.

  @Description
    Toggles the GPIO pin, RA0, using LATAbits.LATA0.

  @Preconditions
    The RA0 must be set to an output.

  @Returns
    None.

  @Param
    None.

  @Example
    <code>
    // Toggle RA0
    CURRENT_5_Toggle();
    </code>

*/
#define CURRENT_5_Toggle()           ( LATAINV = (1 << 0) )
/**
  @Summary
    Reads the value of the GPIO pin, RA0.

  @Description
    Reads the value of the GPIO pin, RA0.

  @Preconditions
    None.

  @Returns
    None.

  @Param
    None.

  @Example
    <code>
    uint16_t portValue;

    // Read RA0
    postValue = CURRENT_5_GetValue();
    </code>

*/
#define CURRENT_5_GetValue()         PORTAbits.RA0
/**
  @Summary
    Configures the GPIO pin, RA0, as an input.

  @Description
    Configures the GPIO pin, RA0, as an input.

  @Preconditions
    None.

  @Returns
    None.

  @Param
    None.

  @Example
    <code>
    // Sets the RA0 as an input
    CURRENT_5_SetDigitalInput();
    </code>

*/
#define CURRENT_5_SetDigitalInput()   ( TRISASET = (1 << 0) )
/**
  @Summary
    Configures the GPIO pin, RA0, as an output.

  @Description
    Configures the GPIO pin, RA0, as an output.

  @Preconditions
    None.

  @Returns
    None.

  @Param
    None.

  @Example
    <code>
    // Sets the RA0 as an output
    CURRENT_5_SetDigitalOutput();
    </code>

*/
#define CURRENT_5_SetDigitalOutput()   ( TRISACLR = (1 << 0) )
/**
  @Summary
    Sets the GPIO pin, RA1, high using LATAbits.LATA1.

  @Description
    Sets the GPIO pin, RA1, high using LATAbits.LATA1.

  @Preconditions
    The RA1 must be set to an output.

  @Returns
    None.

  @Param
    None.

  @Example
    <code>
    // Set RA1 high (1)
    CURRENT_4_SetHigh();
    </code>

*/
#define CURRENT_4_SetHigh()          ( LATASET = (1 << 1) )
/**
  @Summary
    Sets the GPIO pin, RA1, low using LATAbits.LATA1.

  @Description
    Sets the GPIO pin, RA1, low using LATAbits.LATA1.

  @Preconditions
    The RA1 must be set to an output.

  @Returns
    None.

  @Param
    None.

  @Example
    <code>
    // Set RA1 low (0)
    CURRENT_4_SetLow();
    </code>

*/
#define CURRENT_4_SetLow()           ( LATACLR = (1 << 1) )
/**
  @Summary
    Toggles the GPIO pin, RA1, using LATAbits.LATA1.

  @Description
    Toggles the GPIO pin, RA1, using LATAbits.LATA1.

  @Preconditions
    The RA1 must be set to an output.

  @Returns
    None.

  @Param
    None.

  @Example
    <code>
    // Toggle RA1
    CURRENT_4_Toggle();
    </code>

*/
#define CURRENT_4_Toggle()           ( LATAINV = (1 << 1) )
/**
  @Summary
    Reads the value of the GPIO pin, RA1.

  @Description
    Reads the value of the GPIO pin, RA1.

  @Preconditions
    None.

  @Returns
    None.

  @Param
    None.

  @Example
    <code>
    uint16_t portValue;

    // Read RA1
    postValue = CURRENT_4_GetValue();
    </code>

*/
#define CURRENT_4_GetValue()         PORTAbits.RA1
/**
  @Summary
    Configures the GPIO pin, RA1, as an input.

  @Description
    Configures the GPIO pin, RA1, as an input.

  @Preconditions
    None.

  @Returns
    None.

  @Param
    None.

  @Example
    <code>
    // Sets the RA1 as an input
    CURRENT_4_SetDigitalInput();
    </code>

*/
#define CURRENT_4_SetDigitalInput()   ( TRISASET = (1 << 1) )
/**
  @Summary
    Configures the GPIO pin, RA1, as an output.

  @Description
    Configures the GPIO pin, RA1, as an output.

  @Preconditions
    None.

  @Returns
    None.

  @Param
    None.

  @Example
    <code>
    // Sets the RA1 as an output
    CURRENT_4_SetDigitalOutput();
    </code>

*/
#define CURRENT_4_SetDigitalOutput()   ( TRISACLR = (1 << 1) )
/**
  @Summary
    Sets the GPIO pin, RA10, high using LATAbits.LATA10.

  @Description
    Sets the GPIO pin, RA10, high using LATAbits.LATA10.

  @Preconditions
    The RA10 must be set to an output.

  @Returns
    None.

  @Param
    None.

  @Example
    <code>
    // Set RA10 high (1)
    RELAY_3_SetHigh();
    </code>

*/
#define RELAY_3_SetHigh()          ( LATASET = (1 << 10) )
/**
  @Summary
    Sets the GPIO pin, RA10, low using LATAbits.LATA10.

  @Description
    Sets the GPIO pin, RA10, low using LATAbits.LATA10.

  @Preconditions
    The RA10 must be set to an output.

  @Returns
    None.

  @Param
    None.

  @Example
    <code>
    // Set RA10 low (0)
    RELAY_3_SetLow();
    </code>

*/
#define RELAY_3_SetLow()           ( LATACLR = (1 << 10) )
/**
  @Summary
    Toggles the GPIO pin, RA10, using LATAbits.LATA10.

  @Description
    Toggles the GPIO pin, RA10, using LATAbits.LATA10.

  @Preconditions
    The RA10 must be set to an output.

  @Returns
    None.

  @Param
    None.

  @Example
    <code>
    // Toggle RA10
    RELAY_3_Toggle();
    </code>
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

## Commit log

2015-09-16 fixed A/D clock in powerControl.c
2015-11-19 added micros for LEDs added support to disable to current sensing
2015-12-22 change message structure sent by master rename Power directory
2017-04-23 continued work on abstraction, focus on led and adc
2017-05-06 refactored power
2017-10-30 included board design
    [Analog-Input-Card.kicad_pcb, Analog-Input-Card.sch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]
2017-10-30 removed unneeded boards
    [Level.sch]
2017-10-30 removed modules without firmware
    [Serial-Interface-Card.kicad_pcb, Serial-Interface-Card.sch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]
2017-10-31 started ananlog input revision 2
    [Analog-Input-Card.sch]
2017-11-01 finished rev 2 for analog input
    [Analog-Input-Card.kicad_pcb, Analog-Input-Card.sch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]
2017-11-01 documentation for rev 2 analog input
    [Analog-Input-Card.sch]
2017-11-10 work on ai v2
    [Analog-Input-Card.sch]
2017-11-10 cleanup symbolic links
    [Analog-Input-Card.csv, Analog-Input-Card.ods]
2017-11-11 started i2c driver
2017-11-12 worked on i2c driver and board design
    [Analog-Input-Card.csv, Analog-Input-Card.kicad_pcb, Analog-Input-Card.ods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]
2017-11-13 started development with PIC32MM
    [Analog-Input-Card.ods, Analog-Input-Card.sch, AquaPic-Bus-Design.xlsx]
2017-11-16 Added some documentation
    [AquaPicBusCommunicationStructure.xlsx]
2017-11-16 finished board layout for ai
    [Analog-Input-Card.kicad_pcb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]
2017-11-19 finished rough alpha firmware for analog input
    [lowpass.ods]
2017-11-23 started working on compiling
    [AquaPicBusCommunicationPackets.ods, AquaPicBusCommunicationStructure.xlsx, lowpass.ods]
2017-11-24 finished command line building and fixing other cards
    [AquaPicBusCommunicationPackets.ods]
2017-11-24 fixed silkscreen on analog input
    [Analog-Input-Card.kicad_pcb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]
2017-11-24 regenerated gerbers
2017-11-24 added ai schematic image
2017-11-24 cleaning up a few things
    [Analog-Input-Card.sch, phOrpCard.csv]
2017-11-24 started work on pH/ORP card redesign
    [_saved_pH-ORP-Card.sch, pH-ORP-Card.kicad_pcb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]
2017-11-24 worked on pH ORP board layout
    [_saved_pH-ORP-Card.sch, pH-ORP-Card.kicad_pcb, pH-ORP-Card.sch]
2017-11-25 added firmware for the pH ORP Card
    [Analog-Input-Card-B.Cu.gbl, Analog-Input-Card-B.Mask.gbs, Analog-Input-Card-B.SilkS.gbo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]
2017-11-25 finished pH ORP BOM
    [Analog-Input-Card.ods, pH-ORP-Card.ods, pH-ORP-Card.xlsx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]
2017-11-25 something changed in schematic
    [pH-ORP-Card.sch]
2017-11-25 fixed led pin startup state
    [main.c]
2017-11-26 added enable disable for ph isolation
    [Analog-Input-Card.ods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]
2017-11-26 kicad updating something
    [pH-ORP-Card.sch]
2017-11-26 starting refactoring analog output
    [Analog-Output-Card.kicad_pcb, Analog-Output-Card.sch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]
2017-12-01 fixed pinout on analog input card
    [Analog-Input-Card.kicad_pcb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]
2017-12-02 working on Analog Output card
    [Analog-Input-Card.kicad_pcb, Analog-Output-Card.kicad_pcb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]
2017-12-03 worked on Analog Output Cardboard layout finished
    [Analog-Input-Card.ods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]
2017-12-03 fixed setting pwm value
    [main.c]
2017-12-03 removed Analog-Output-Card.csv
    [Analog-Output-Card.csv]
2017-12-03 added EEPROM simulation
    [AquaPicBusCommunicationPackets.ods]
2017-12-03 fixed uninitialized nvm reading
    [main.c]
2017-12-10 refactored Digital Input to PIC32
    [Analog-Input-Card.sch, Analog-Output-Card.sch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]
2017-12-10 updated digital input bom
    [Digital-Input-Card.ods, Digital-Input-Card.xlsx]
2017-12-10 worked on charlieplexed led circuit design
    [Digital-Input-Card.kicad_pcb, Digital-Input-Card.ods, Digital-Input-Card.sch]
2017-12-12 working on refactoring power to PIC32
    [Power.kicad_pcb, Power.sch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]
2017-12-13 working on power refactor
    [Power-old.kicad_pcb, Power.kicad_pcb, Power.sch]
2017-12-17 finished alpha power firmware
2017-12-17 fixed apb addressing
    [AquaPicBusCommunicationPackets.ods]
2017-12-18 working on power pcb
    [Power-old.kicad_pcb, Power.kicad_pcb, Power.sch]
2018-03-08 must have made changes to some schematics
    [Analog-Input-Card.sch, pH-ORP-Card.sch]
2018-06-05 finished power board layout and fixed pin mappings
    [Power-B.Cu.gbl, Power-B.Mask.gbs, Power-B.SilkS.gbo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]
2018-06-06 added power bom
    [Power.ods, Power.sch]
2018-07-31 fixed placement on boards so everything is mostly in the same spot
    [Analog-Input-Card.kicad_pcb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]
2018-08-14 more work on uniformity between boards
    [Analog-Input-Card-B.Cu.gbl, Analog-Input-Card-B.Mask.gbs, Analog-Input-Card-B.SilkS.gbo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]
2018-08-24 Cleanup on Power PCB
    [Power.kicad_pcb]
2018-09-30 working on analog input bom
    [Analog-Input-Card.ods]
2018-09-30 upgrade pH ORP to KiCAD 5
    [pH-ORP-Card.sch]
2018-09-30 changed power supply isolation to n channel mosfet, schematic is now bom
    [pH-ORP-Card-B.Cu.gbl, pH-ORP-Card-B.Mask.gbs, pH-ORP-Card-B.SilkS.gbo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]
2018-09-30 removed tracking bom and schematics
    [Analog-Input-Card.ods, Analog-Output-Card.ods, Digital-Input-Card.ods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]
2018-09-30 changed power supply switch from p channel to n channel
    [pH-ORP-Card-B.Cu.gbl, pH-ORP-Card-B.Mask.gbs, pH-ORP-Card-B.SilkS.gbo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]
2018-09-30 migrated digital input to KiCAD 5
    [Digital-Input-Card-B.Cu.gbl, Digital-Input-Card-B.Mask.gbs, Digital-Input-Card-B.SilkS.gbo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]
2018-09-30 fixed icsp footprint
    [Digital-Input-Card.sch]
2018-10-18 updated analog input to kicad 5
    [Analog-Input-Card.sch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]
2018-10-18 renamed analog input and output directories
    [Analog-Input-Card-B.Cu.gbl, Analog-Input-Card-B.Mask.gbs, Analog-Input-Card-B.SilkS.gbo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]
2018-10-18 analog output bom is not controlled by schematic
    [Analog-Output-Card.sch]
2018-10-18 analog input bom is now controlled by schematic
    [Analog-Input-Card.sch]
2018-10-18 renamed Power directory
    [Power-B.Cu.gbl, Power-B.Mask.gbs, Power-B.SilkS.gbo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]
2018-10-18 Power bom is now controlled by schematic
    [Power.sch]
2018-10-18 generated BOMs
    [Power.sch]

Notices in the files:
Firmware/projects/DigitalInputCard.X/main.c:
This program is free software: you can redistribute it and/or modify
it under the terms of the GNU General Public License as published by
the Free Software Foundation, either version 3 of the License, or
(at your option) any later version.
